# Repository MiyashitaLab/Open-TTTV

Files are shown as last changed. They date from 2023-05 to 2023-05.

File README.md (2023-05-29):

# Open-TTTV
WISS2022で発表したOpen-TTTVの作り方についての記事です
<br>
https://research.miyashita.com/papers/D265
maxresdefault

## 必要なもの
・[本リポジトリ内のSTLファイル](https://github.com/MiyashitaLab/Open-TTTV/tree/main/STL)<br>
　ファイルの最後に数字がある場合はその数印刷してください<br>
　Open-TTTVを傾ける台は噴霧対象に応じて使い分けてください<br>
・[無印良品　ポリエチレン小分けボトル　スプレータイプ　15ml](https://www.muji.com/jp/ja/store/cmdty/detail/4550344579145)　190円 ×9<br>
・[タカハ機工　CB12500045 プッシュソレノイド DC6V仕様](https://www.monotaro.com/p/4063/8168/)　2590円<br>
・[FEETECH FT1117M ミニPWMサーボ](https://ssci.to/7118)　957円<br>
・[スイッチングＡＣアダプター9V2A　AD-A90P200](https://akizukidenshi.com/catalog/g/gM-08309/)　1100円<br>
・[M5Stack用ME3116AM6G搭載 5V 降圧コンバータユニット](https://ssci.to/7481)　561円<br>
・[M5Stack BAVG2ソケット](https://ssci.to/7234)　429円<br>
・[M5Stack用拡張ハブユニット [U006]](https://ssci.to/5696)　517円<br>
・[Solenoid UNIT](https://ssci.to/8517)　660円<br>
・[ATOM Lite](https://ssci.to/6262)　1342円<br>
・[GROVE - サーボ用2分岐ケーブル (5本セット)](https://ssci.to/1250)　847円<br>
・[SARASA](https://www.zebra.co.jp/pro/detail/sarasa-clip/?tab=lineup_sarasa-clip_05) 110円×9<br>
・[2.1ｍｍ ΦＤＣ分岐ケーブル](https://akizukidenshi.com/catalog/g/gC-06723/)　350円<br>
・[皿頭小ねじ(ステンレス)](https://www.monotaro.com/p/0550/8465/)　M3×30　1つ<br>
・[皿頭小ねじ(ステンレス)](https://www.monotaro.com/p/0550/8535/)　M4×10　4つ<br>
・[皿頭小ねじ(ステンレス)](https://www.monotaro.com/p/0550/8754/)　M5×15　4つ<br>
・[六角ナット　2種(ステンレス)](https://www.monotaro.com/p/4221/7585/)　M5　4つ<br>
※サイズ・規格等が同じであれば上記リンク以外のものでも構いません
※価格は2023年5月28日時点での価格です。

## 作り方

https://github.com/MiyashitaLab/Open-TTTV/assets/75302406/29ad6028-4944-4c81-b780-6740f61415f1

より詳しい作り方は[こちらのページ](https://github.com/MiyashitaLab/Open-TTTV/blob/main/HowToMake.md)を参照してください<br>
※必要に応じてケーブルの処理、接着等を行ってください<br>
※スプレーボトル内部のばねをSARASAのばねと交換してください<br>

## 内部の組み立て
内部の組み立ては以下の図を参照してください<br>
Open-TTTV2

## 使用方法
①ATOM LiteにCode内のプログラムを書き込む<br>
　※コンパイルには"M5Atom"、"ESP32Servo"のライブラリが必要です<br>
　※data内のファイルはArduinoで書き込みするだけでは転送されず、別途SPIFFSアップローダを使って転送する必要があります<br>
 　　詳細は[こちらのページ](https://www.mgo-tec.com/blog-entry-spiffs-uploader-plugin-arduino-esp32.html)を参考にしてください<br>
②スマホからATOM Liteに接続する<br>
　設定画面からWi-fiの接続先を検索し、Open-TTTVと接続します。初期パスワードは"opentttv"です。<br>
③ブラウザでIPアドレスを入力しページを開く<br>
　任意のブラウザを立ち上げ、IPアドレスを入力して下さい<br>
④任意に味を調整しSENDボタンを押す<br>
　任意の画像を選択、味を調整し、画面下部にあるTransformボタンを押すことでOpen-TTTVから味が出力されます。<br>
 

## License

The MIT License(MIT)

Copyright (c) [2023] [MiyashitaLab]

Permission is hereby granted, free of charge, to any person obtaining a copy
of this software and associated documentation files (the "Software"), to deal
in the Software without restriction, including without limitation the rights
to use, copy, modify, merge, publish, distribute, sublicense, and/or sell
copies of the Software, and to permit persons to whom the Software is
furnished to do so, subject to the following conditions:

The above copyright notice and this permission notice shall be included in all
copies or substantial portions of the Software.

THE SOFTWARE IS PROVIDED "AS IS", WITHOUT WARRANTY OF ANY KIND, EXPRESS OR
IMPLIED, INCLUDING BUT NOT LIMITED TO THE WARRANTIES OF MERCHANTABILITY,
FITNESS FOR A PARTICULAR PURPOSE AND NONINFRINGEMENT. IN NO EVENT SHALL THE
AUTHORS OR COPYRIGHT HOLDERS BE LIABLE FOR ANY CLAIM, DAMAGES OR OTHER
LIABILITY, WHETHER IN AN ACTION OF CONTRACT, TORT OR OTHERWISE, ARISING FROM,
OUT OF OR IN CONNECTION WITH THE SOFTWARE OR THE USE OR OTHER DEALINGS IN THE
SOFTWARE.

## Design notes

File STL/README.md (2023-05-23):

# 印刷について
本フォルダ内にあるSTLファイルを印刷してください。芯結合部のみ4つ印刷する必要があります。<br>
また、傾ける台A、Bは噴霧対象に応じて必要があれば印刷をしてください。

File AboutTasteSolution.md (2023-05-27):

# 味溶液について
基本五味(塩味、酸味、甘味、旨味、苦味)や辛味、渋味といった味溶液を自由に搭載することで様々なバリエーションの味を再現することができます。また、着色料を溶かした水溶液を搭載することで噴霧対象の色味を変化させることも可能です。<br>
以下は使用した溶液の例です。カスタマイズすることで様々な味や見た目を再現することが可能です。<br>

例)着色溶液を使用する場合<br>
***塩味：塩化ナトリウム<br>
酸味：クエン酸<br>
甘味：スクロース<br>
苦味：炭酸カリウム<br>
旨味：グルタミン酸ナトリウム<br>
着色溶液 青：食用色素 青<br>
着色溶液 赤：食用色素 赤<br>
着色溶液 黄：食用色素 黄<br>
着色溶液 黒：食用色素 黒***<br>

例)着色溶液を使用しない場合<br>
***塩味：塩化ナトリウム<br>
酸味A：クエン酸<br>
酸味B：乳酸<br>
甘味A：スクロース<br>
甘味B：フルクトース<br>
苦味A：炭酸カリウム<br>
苦味B：アルギニン<br>
旨味：グルタミン酸ナトリウム<br>
辛味：カプサイシン***<br>

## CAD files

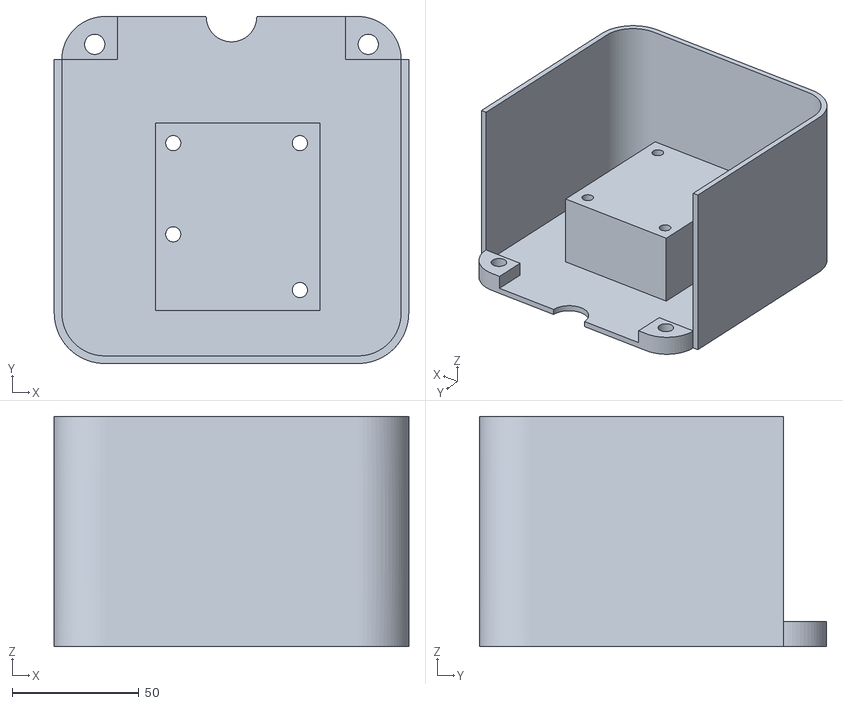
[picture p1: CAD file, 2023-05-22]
STL/筐体.stl
140.0 x 137.0 x 91.0

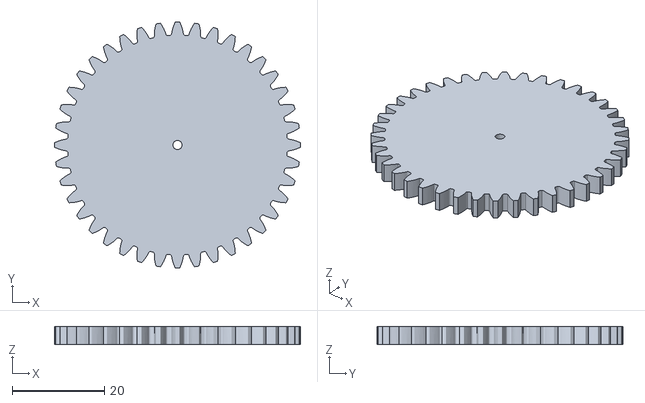
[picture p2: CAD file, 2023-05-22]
STL/サーボモータ用ギア.stl
53.3 x 53.3 x 4.00

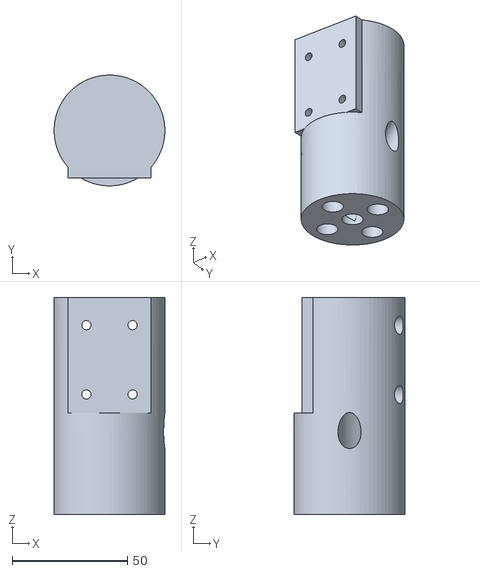
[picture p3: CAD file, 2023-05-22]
STL/芯上部.stl
48.0 x 48.0 x 94.0

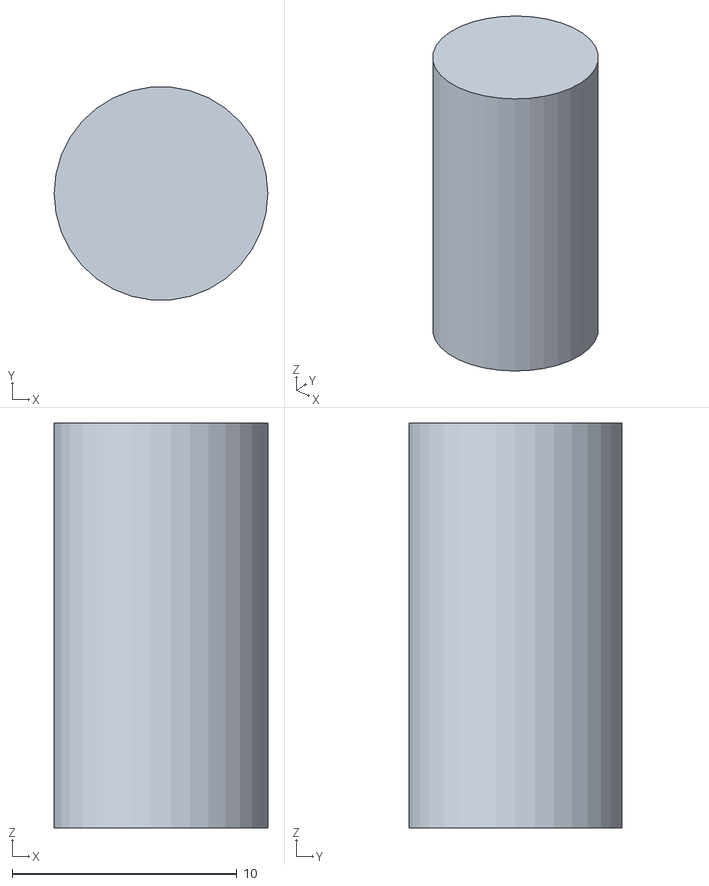
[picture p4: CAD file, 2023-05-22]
STL/芯結合部_4.stl
9.50 x 9.46 x 18.0

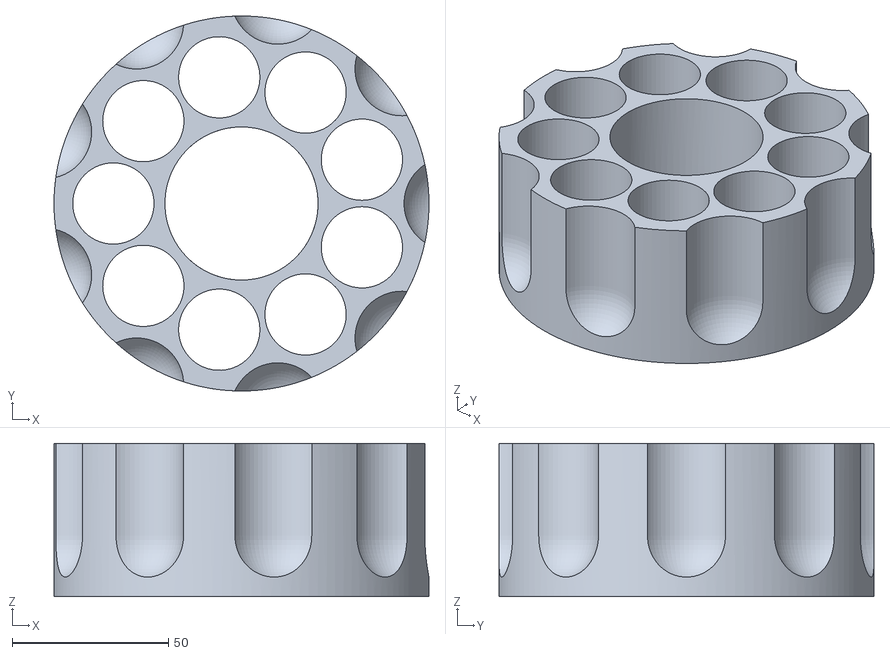
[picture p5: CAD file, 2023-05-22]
STL/スプレーボトルホルダー.stl
120.0 x 120.0 x 49.0

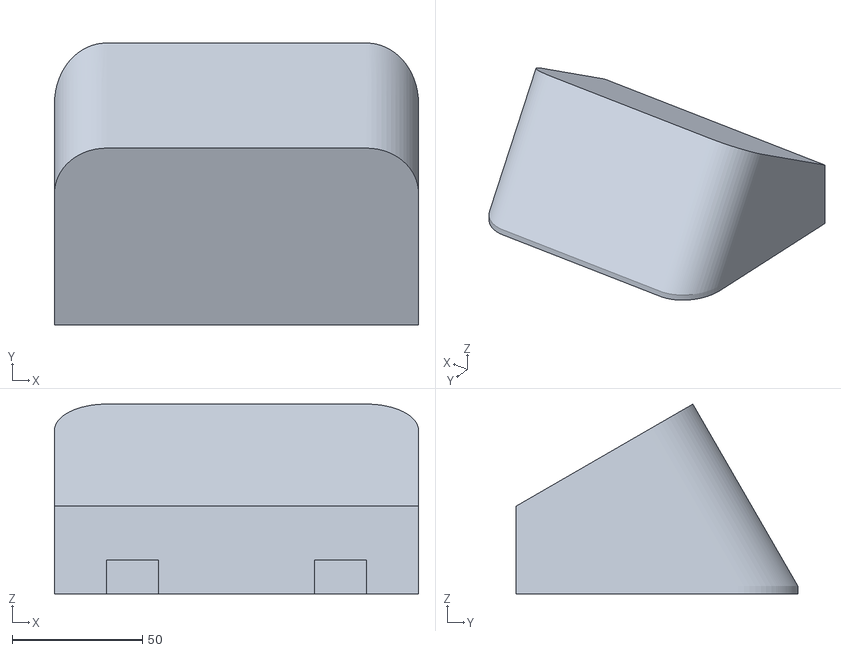
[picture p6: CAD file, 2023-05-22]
STL/傾ける台B.stl
140.0 x 108.4 x 73.0

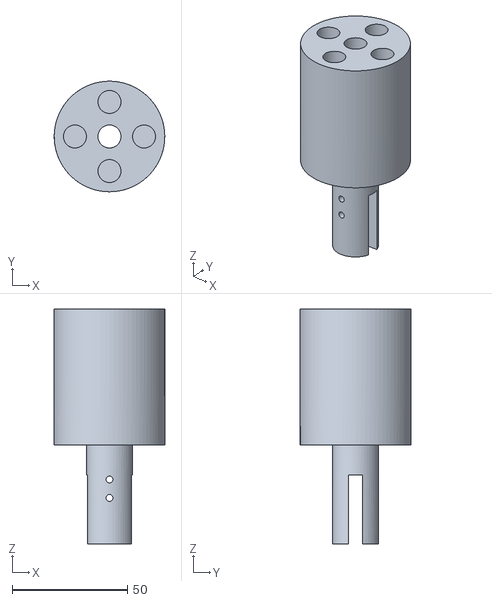
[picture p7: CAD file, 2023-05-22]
STL/芯下部.stl
48.0 x 48.0 x 102.0

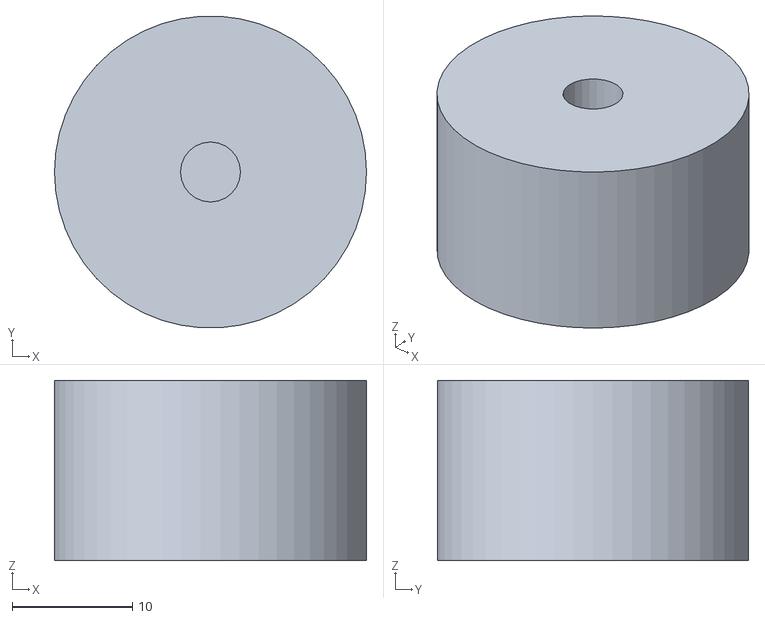
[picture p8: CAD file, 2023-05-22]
STL/ソレノイド先端.stl
26.0 x 25.9 x 15.0

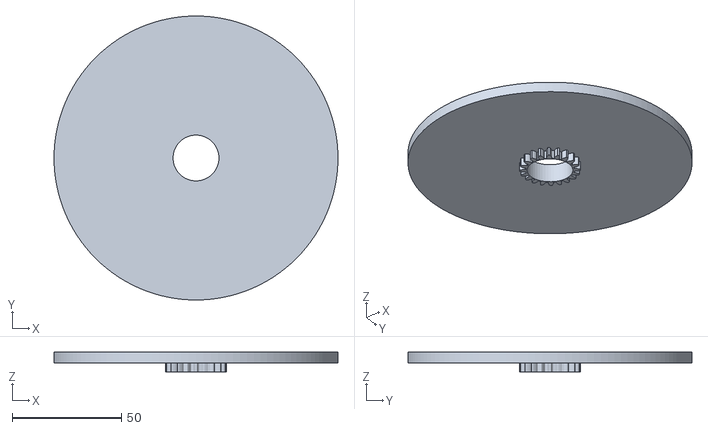
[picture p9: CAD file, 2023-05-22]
STL/回転台.stl
130.0 x 130.0 x 9.00

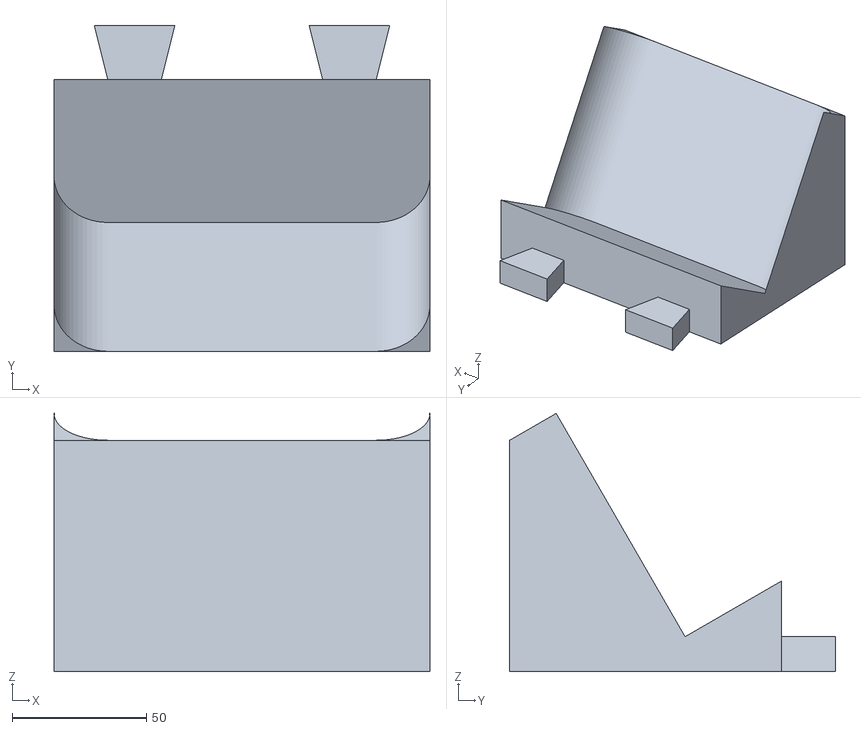
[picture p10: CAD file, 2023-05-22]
STL/傾ける台A.stl
140.0 x 121.2 x 96.1

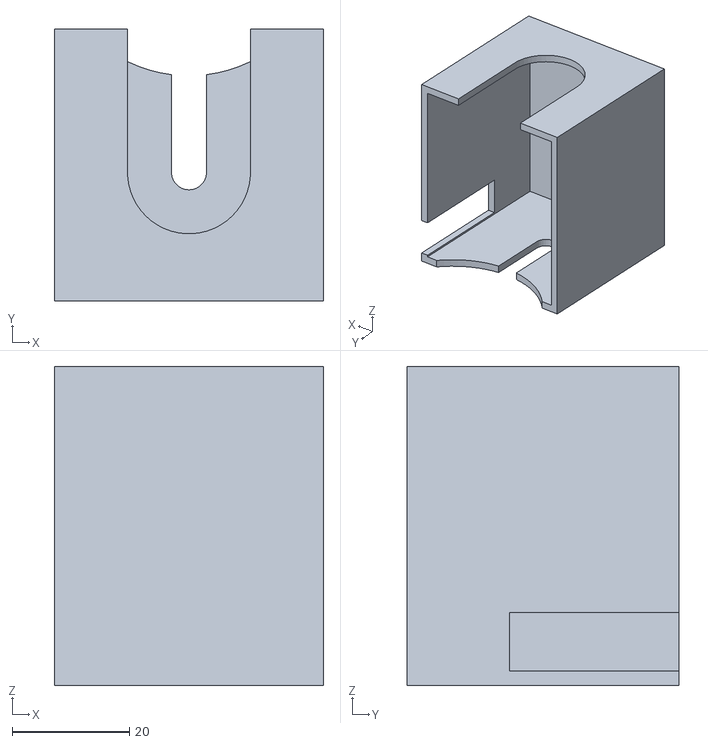
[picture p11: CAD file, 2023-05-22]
STL/ソレノイドカバーA.stl
46.0 x 46.5 x 54.5

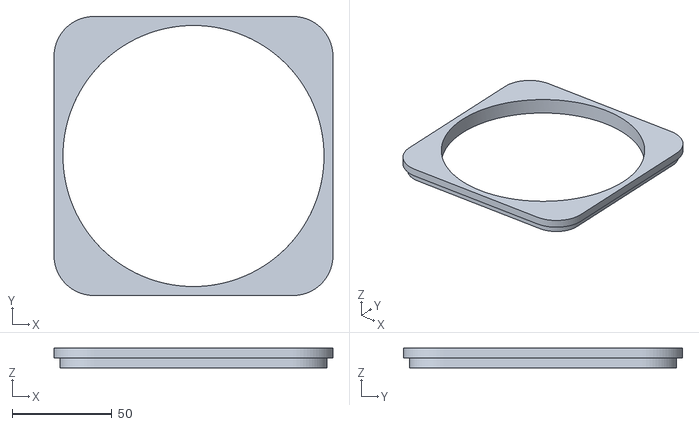
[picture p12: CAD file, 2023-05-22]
STL/筐体蓋.stl
140.0 x 140.0 x 10.0

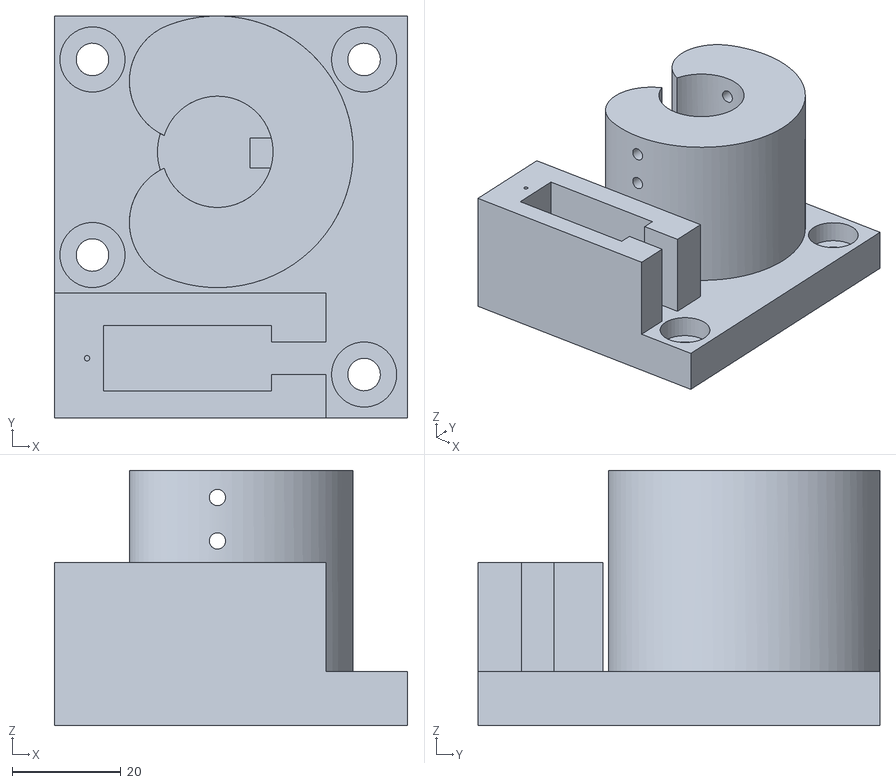
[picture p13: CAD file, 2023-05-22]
STL/サーボモータ土台.stl
65.0 x 74.0 x 47.0

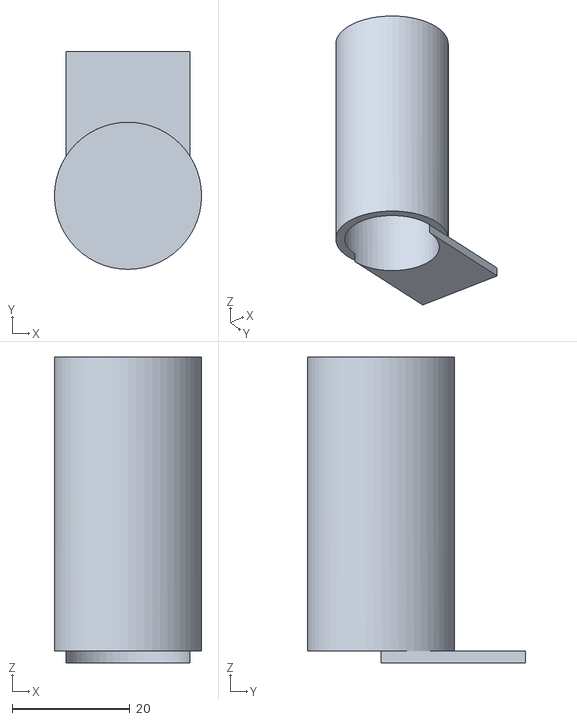
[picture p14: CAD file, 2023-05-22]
STL/ソレノイドカバーB.stl
25.0 x 37.0 x 52.0

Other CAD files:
STL/筐体裏扉.stl

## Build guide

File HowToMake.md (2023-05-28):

# Open-TTTVの詳しい作り方

## 事前準備
本リポジトリ内にあるSTLデータを3Dプリンタで出力します。<br>
ファイルの最後に数字がある場合はその数を印刷してください。<br>
組み立てに際し、以下のものが必要になります。<br>
・ねじ(M3×30 1つ、M4×10 4つ、M5×15 4つ)<br>
・ナット(M5 4つ)<br>
・ソレノイド<br>
・サーボモータ(FT1117M)<br>
・接着剤<br>
・ドライバ<br>
## 作り方
### 1.ソレノイドの芯をつくる
芯下部、芯上部を芯結合部×4で固定します。必要に応じて接着剤を使用してください。 

### 2.ソレノイドを芯に固定する
ねじ(M4×10)でソレノイドを芯に固定します。 ソレノイドの導線は芯内部へと入れて芯の下から導線が出るようにしてください。


### 3.ソレノイドにカバーを付ける
ソレノイドカバーA、B及びソレノイド先端をソレノイドに装着します。


### 4.スプレーボトルホルダーの装着
スプレーボトルホルダーを回転台に接着剤で固定し、芯へ差し込みます。


### 5.筐体内部の組み立て
サーボモータ(FT1117M)をサーボモータ土台に装着します。同時にサーボモータにサーボモータ用ギアを接着してください。


### 6.芯をサーボモータ土台に差し込む
3.までに作った芯をサーボモータ土台に差し込みます。この際にソレノイドがサーボモータ上に来るように差し込むようにしてください。


### 7.サーボモータ土台にねじで固定
ねじ(M3×30)で芯をサーボモータ土台に固定します。この時に芯内部を通しているソレノイドの導線を傷つけないように注意して下さい。


### 8.筐体に取り付ける
7.までに作ったものを筐体にねじ(M5×15)、ナット(M5)で固定します。


### 9.筐体裏扉を装着
8.までに作ったものに筐体裏扉を装着します。事前に内部の組み立てが終了している際はケーブルを挟まないように注意してください。
]

### 10.蓋をする
9.までに作ったものに筐体蓋を取り付けて完成です。


### 完成図


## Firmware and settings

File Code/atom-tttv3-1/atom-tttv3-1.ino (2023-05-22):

#include "WiFi.h"
#include <WebServer.h>
#include <uri/UriBraces.h>
#include <ESPmDNS.h>
#include "M5Atom.h"
#include <SPIFFS.h>
#include <ESP32Servo.h>


// サーバー設定ポート80で接続
WebServer server(80);

void setup() {
  SPIFFS.begin();
  M5.begin(true, false, true);
  delay(50);

  // connectWiFi(); //STAモード
  setupAP(); //APモード
  
  setupServer();
  setupDriver();
}

void loop() {
  M5.update();
  server.handleClient();  //クライアントからのアクセス確認
  delay(50);              //遅延時間（ms）
}

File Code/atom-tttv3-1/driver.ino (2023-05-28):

TaskHandle_t th[2];

Servo servo;

const uint8_t cylinderServoPin = 26;
const uint8_t pushSolenoidPin = 32;
const uint8_t pushSolenoidPwmChannel = 15;

//ボトルの本数を設定
const int bottleNum = 9;

//各indexごとのサーボ設定角度を指定
const int offset = 0;
const int angleDiv = 20;
//ここの値を適宜調整してスプレーがソレノイド直下に来るように調整してください
const int bottleIndexToAngle[] = {
  offset ,
  offset + angleDiv * 1 ,
  offset + angleDiv * 2 ,
  offset + angleDiv * 3 ,
  offset + angleDiv * 4 ,
  offset + angleDiv * 5 ,
  offset + angleDiv * 6 ,
  offset + angleDiv * 7 ,
  offset + angleDiv * 8 
};

//順にsalty, sour, sweet, bitter, umami, black, cyan, magenta, yellowに対応
//各味の置く場所を変えた場合はここを変える
const int tasteIndexToBottleIndex[] = {0, 1, 2, 3, 4, 5, 6, 7, 8};

//各味のsequence出力順
//0: salty, 1: sour, 2: sweet, 3: bitter, 4: umami, 5: black, 6: cyan, 7: magenta, 8: yellow
const int tasteIndexSequence[] = { 0, 1, 2, 3, 4, 5, 6, 7, 8};

const int solenoidPower = 255;  //0~255 線形では無いかも

void setupDriver() {
  // pinMode(cylinderServoPin, OUTPUT);
  ESP32PWM::allocateTimer(0);
  servo.setPeriodHertz(50);
  servo.attach(cylinderServoPin, 600, 2500);

  pinMode(pushSolenoidPin, OUTPUT);
  ledcSetup(pushSolenoidPwmChannel, 12800, 8);
  ledcAttachPin(pushSolenoidPin, pushSolenoidPwmChannel);

  rotateBottleCylinder(0);
}

void rotateBottleCylinder(int bottleIndex) {
  Serial.print("rotateBottleCylinder: ");
  Serial.println(bottleIndex);

  int angle = bottleIndexToAngle[(bottleIndex + bottleNum) % bottleNum];

  // Atom.SetServoAngle(cylinderServoChannel, angle);
  servo.write(angle);
}

void pushNozzle() {
  pushNozzleTimes(1);
}

int gtimes = 0;

void pushNozzleTimes(int times) {
  Serial.print("pushNozzleTimes: ");
  Serial.println(times);

  gtimes = times;

  //delayするとサーバの応答が止まってしまうので、別コアで処理する
  xTaskCreatePinnedToCore(pushNozzleTimesTask, "pushNozzleTimesTask", 4096, NULL, 2, NULL, 0);
}

void pushNozzleTimesSync(int times) {
  for (int i = 0; i < times; i++) {

    ledcWrite(pushSolenoidPwmChannel, solenoidPower);  //0 ~ 255
    delay(500);
    ledcWrite(pushSolenoidPwmChannel, 0);
    delay(500);
  }
}

void pushNozzleTimesTask(void* timesPointer) {
  //キャストしてポインタからパラメータを取り出し
  int times = gtimes;

  Serial.print("pushNozzleTimesTask times:");
  Serial.println(times);

  pushNozzleTimesSync(times);

  vTaskDelete(NULL);
}

void sequentialPush(int* tastes) {
  for (int i = 0; i < bottleNum; i++) {
    int tasteIndex = tasteIndexSequence[i];
    rotateBottleCylinder(tasteIndexToBottleIndex[tasteIndex]);
    delay(2000);
    pushNozzleTimesSync(tastes[tasteIndex]);
    delay(2000);
  }
}

CRGB color = 0x000000;
void setStatusLED(CRGB _color) {
  color = _color;
  M5.dis.drawpix(0, color);
}


void blinkLED() {
  xTaskCreatePinnedToCore(blinkLEDTask, "blinkLEDTask", 4096, NULL, 2, NULL, 0);
}

void blinkLEDTask(void* param) {
  M5.dis.drawpix(0, 0x000000);
  delay(100);
  M5.dis.drawpix(0, color);
  delay(100);

  M5.dis.drawpix(0, 0x000000);
  delay(100);
  M5.dis.drawpix(0, color);

  vTaskDelete(NULL);
}
